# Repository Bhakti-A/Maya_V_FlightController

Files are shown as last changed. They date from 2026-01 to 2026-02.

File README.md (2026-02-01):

# Maya_V Flight Controller

This is a custom flight controller PCB designed for drones.

## PCB Preview

<p align="center">
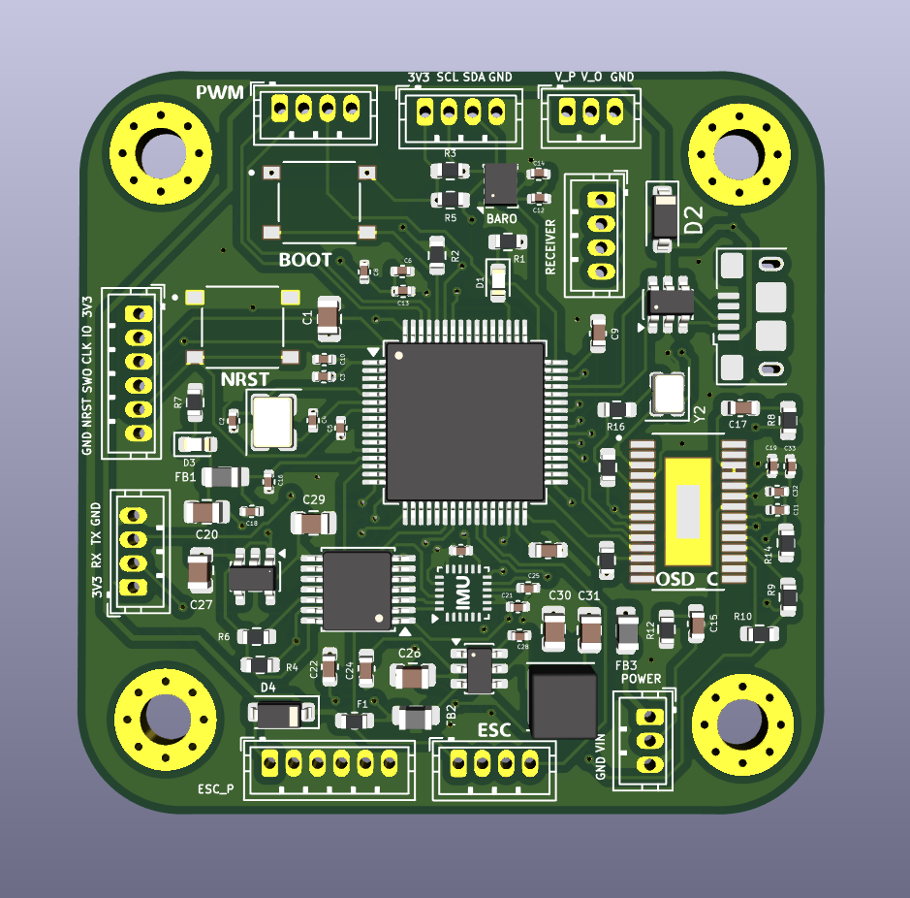
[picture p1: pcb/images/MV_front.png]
  
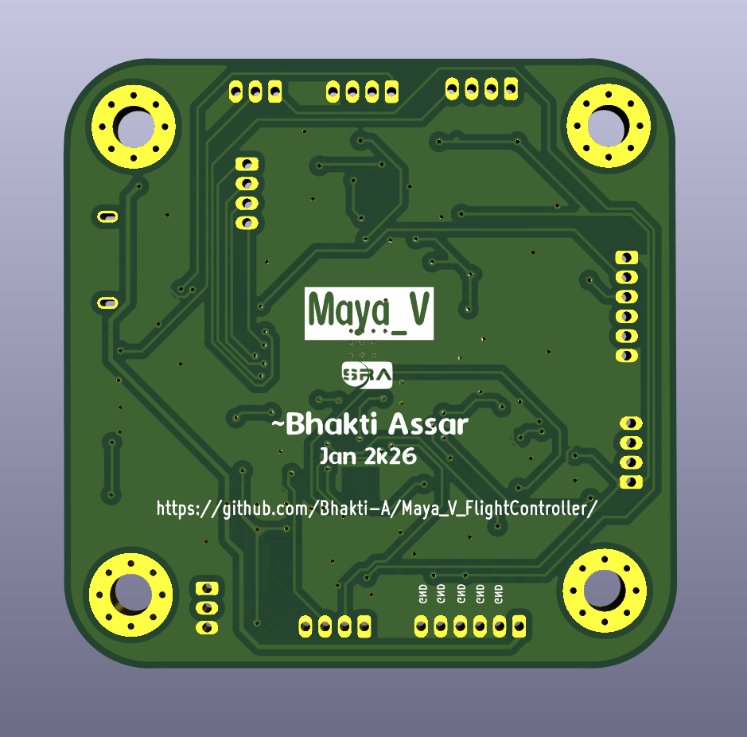
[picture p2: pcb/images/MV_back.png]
  
</p>

## Features

- **Microcontroller:** STM32F405  
- **IMU Sensor:** ICM-20948  
- **Barometer:** BMP280  
- **Video OSD:** MAX7456 
- **ESC Outputs:** 4× PWM channels (with extra PWM expansion)  
- **Communication Interfaces:** UART, I2C, USB  

## Hardware Design

### Schematic & PCB Layout
<p align="center">
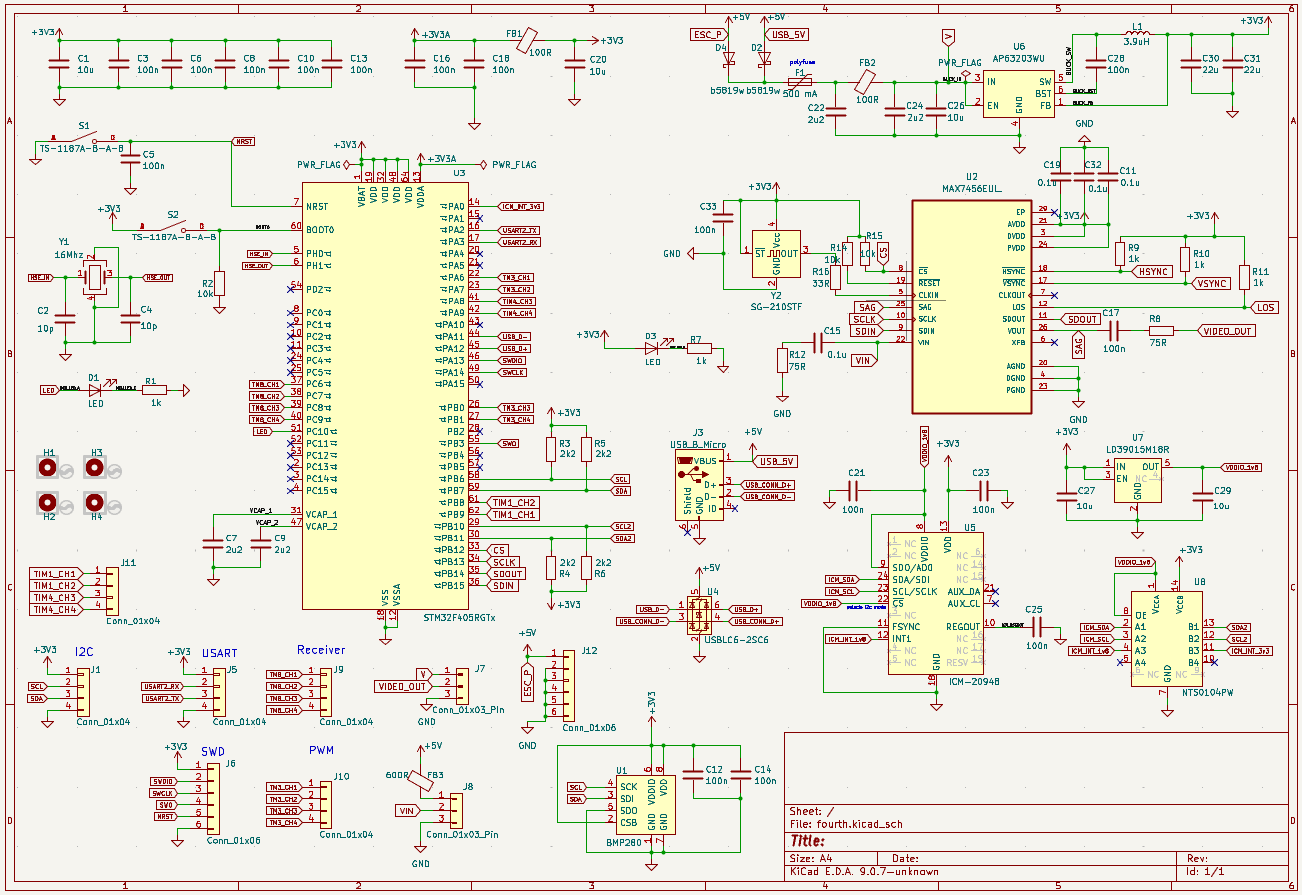
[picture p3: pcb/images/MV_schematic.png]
  
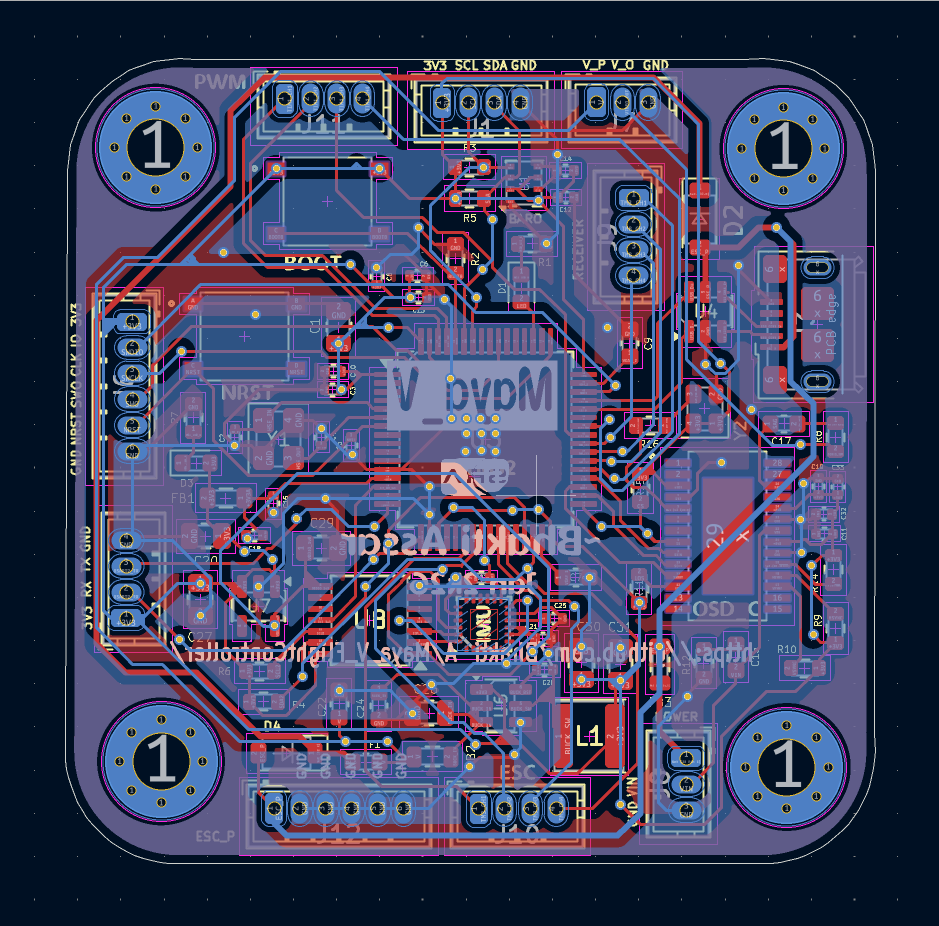
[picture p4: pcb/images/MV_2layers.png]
  
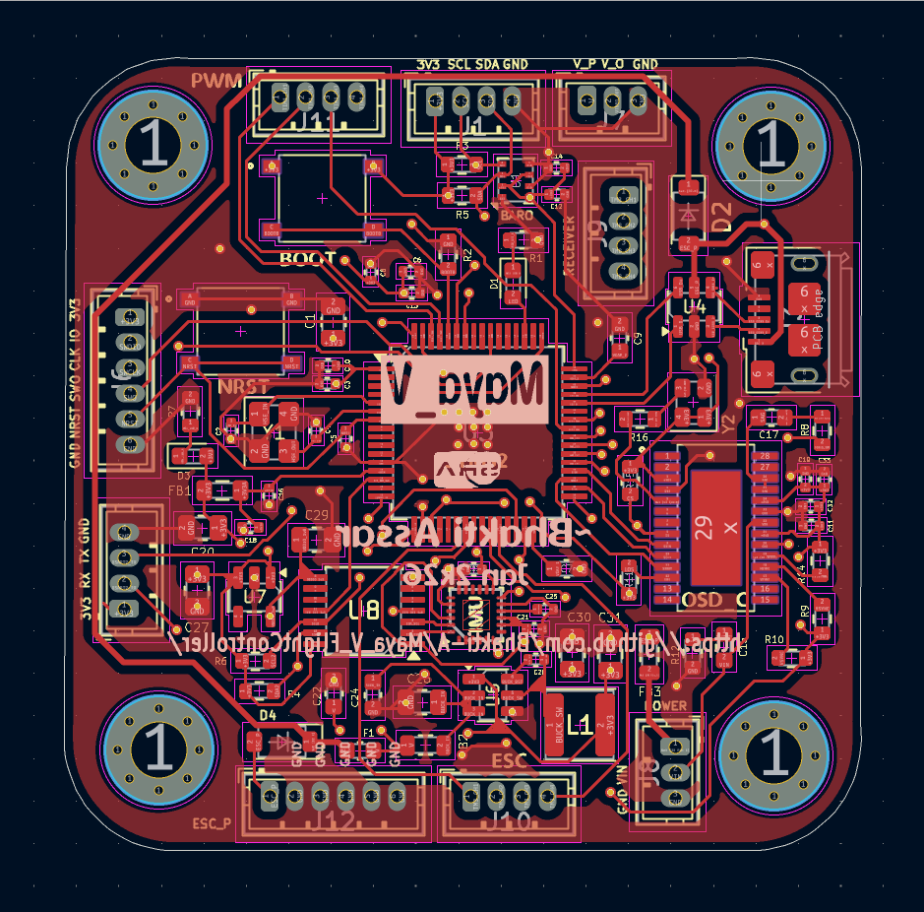
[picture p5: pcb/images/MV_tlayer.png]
  
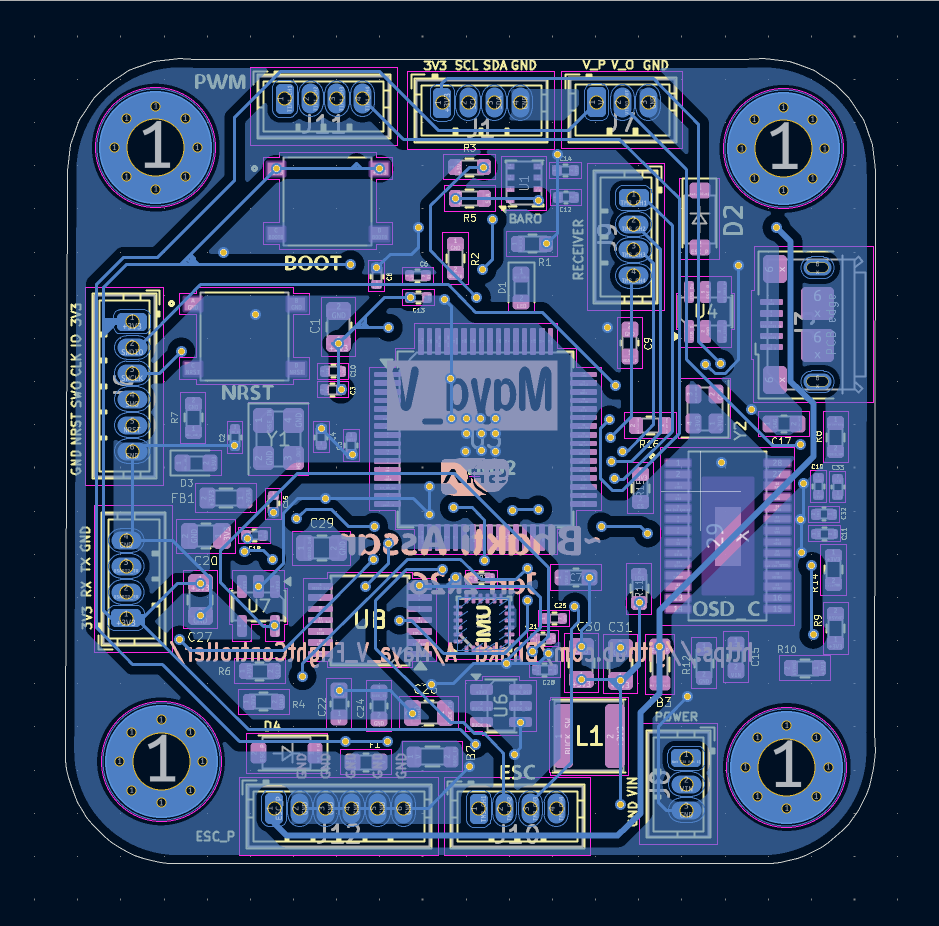
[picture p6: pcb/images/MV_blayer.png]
  
</p>

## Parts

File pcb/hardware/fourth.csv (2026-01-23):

Reference | Qty | Value | DNP | Exclude from BOM | Exclude from Board | Footprint | Datasheet
C1,C20,C26,C27,C29 | 5 | 10u |  |  |  | Capacitor_SMD:C_0805_2012Metric | ~
C2,C4 | 2 | 10p |  |  |  | Capacitor_SMD:C_0402_1005Metric | ~
C3,C5,C6,C8,C10,C12,C13,C14,C16,C18,C21,C23,C25,C28,C33 | 15 | 100n |  |  |  | Capacitor_SMD:C_0402_1005Metric | ~
C7,C9,C22,C24 | 4 | 2u2 |  |  |  | Capacitor_SMD:C_0603_1608Metric | ~
C11,C19,C32 | 3 | 0.1u |  |  |  | Capacitor_SMD:C_0402_1005Metric | ~
C15 | 1 | 0.1u |  |  |  | Capacitor_SMD:C_0603_1608Metric | ~
C17 | 1 | 100n |  |  |  | Capacitor_SMD:C_0603_1608Metric | ~
C30,C31 | 2 | 22u |  |  |  | Capacitor_SMD:C_0805_2012Metric | ~
D1,D3 | 2 | LED |  |  |  | LED_SMD:LED_0603_1608Metric | ~
D2,D4 | 2 | b5819w |  |  |  | Diode_SMD:D_SOD-123 | ~
F1 | 1 | 500 mA |  |  |  | Fuse:Fuse_0603_1608Metric | ~
FB1,FB2 | 2 | 100R |  |  |  | Inductor_SMD:L_0805_2012Metric | ~
FB3 | 1 | 600R |  |  |  | Inductor_SMD:L_0805_2012Metric | ~
H1,H2,H3,H4 | 4 | MountingHole |  | Excluded from BOM |  | MountingHole:MountingHole_3.2mm_M3_Pad_Via | ~
J1,J5,J9,J10,J11 | 5 | Conn_01x04 |  |  |  | Connector_PinSocket_2.00mm:PinSocket_1x04_P2.00mm_Vertical | ~
J3 | 1 | USB_B_Micro |  |  |  | Connector_USB:USB_Micro-B_Amphenol_10118193-0001LF_Horizontal | ~
J6,J12 | 2 | Conn_01x06 |  |  |  | Connector_PinSocket_2.00mm:PinSocket_1x06_P2.00mm_Vertical | ~
J7,J8 | 2 | Conn_01x03_Pin |  |  |  | Connector_PinSocket_2.00mm:PinSocket_1x03_P2.00mm_Vertical | ~
L1 | 1 | 3.9uH |  |  |  | Inductor_SMD:L_Sunlord_SWPA4030S | ~
R1,R7,R9,R10,R11 | 5 | 1k |  |  |  | Resistor_SMD:R_0603_1608Metric | ~
R2,R14,R15 | 3 | 10k |  |  |  | Resistor_SMD:R_0603_1608Metric | ~
R3,R4,R5,R6 | 4 | 2k2 |  |  |  | Resistor_SMD:R_0603_1608Metric | ~
R8,R12 | 2 | 75R |  |  |  | Resistor_SMD:R_0603_1608Metric | ~
R16 | 1 | 33R |  |  |  | Resistor_SMD:R_0603_1608Metric | ~
S1,S2 | 2 | TS-1187A-B-A-B |  |  |  | TS-1187A-B-A-B:SW_TS-1187A-B-A-B
U1 | 1 | BMP280 |  |  |  | Package_LGA:Bosch_LGA-8_2x2.5mm_P0.65mm_ClockwisePinNumbering | https://ae-bst.resource.bosch.com/media/_tech/media/datasheets/BST-BMP280-DS001.pdf
U2 | 1 | MAX7456EUI_ |  |  |  | MAX7456EUI_:SOP65P637X110-28N
U3 | 1 | STM32F405RGTx |  |  |  | Package_QFP:LQFP-64_10x10mm_P0.5mm | https://www.st.com/resource/en/datasheet/stm32f405rg.pdf
U4 | 1 | USBLC6-2SC6 |  |  |  | Package_TO_SOT_SMD:SOT-23-6 | https://www.st.com/resource/en/datasheet/usblc6-2.pdf
U5 | 1 | ICM-20948 |  |  |  | Sensor_Motion:InvenSense_QFN-24_3x3mm_P0.4mm | http://www.invensense.com/wp-content/uploads/2016/06/DS-000189-ICM-20948-v1.3.pdf
U6 | 1 | AP63203WU |  |  |  | Package_TO_SOT_SMD:TSOT-23-6 | https://www.diodes.com/assets/Datasheets/AP63200-AP63201-AP63203-AP63205.pdf
U7 | 1 | LD39015M18R |  |  |  | Package_TO_SOT_SMD:SOT-23-5 | http://www.st.com/resource/en/datasheet/ld39015.pdf
U8 | 1 | NTS0104PW |  |  |  | Package_SO:TSSOP-14_4.4x5mm_P0.65mm
Y1 | 1 | 16Mhz |  |  |  | Crystal:Crystal_SMD_3225-4Pin_3.2x2.5mm | ~
Y2 | 1 | SG-210STF |  |  |  | Oscillator:Oscillator_SMD_SeikoEpson_SG210-4Pin_2.5x2.0mm | https://support.epson.biz/td/api/doc_check.php?mode=dl&lang=en&Parts=SG-210STF

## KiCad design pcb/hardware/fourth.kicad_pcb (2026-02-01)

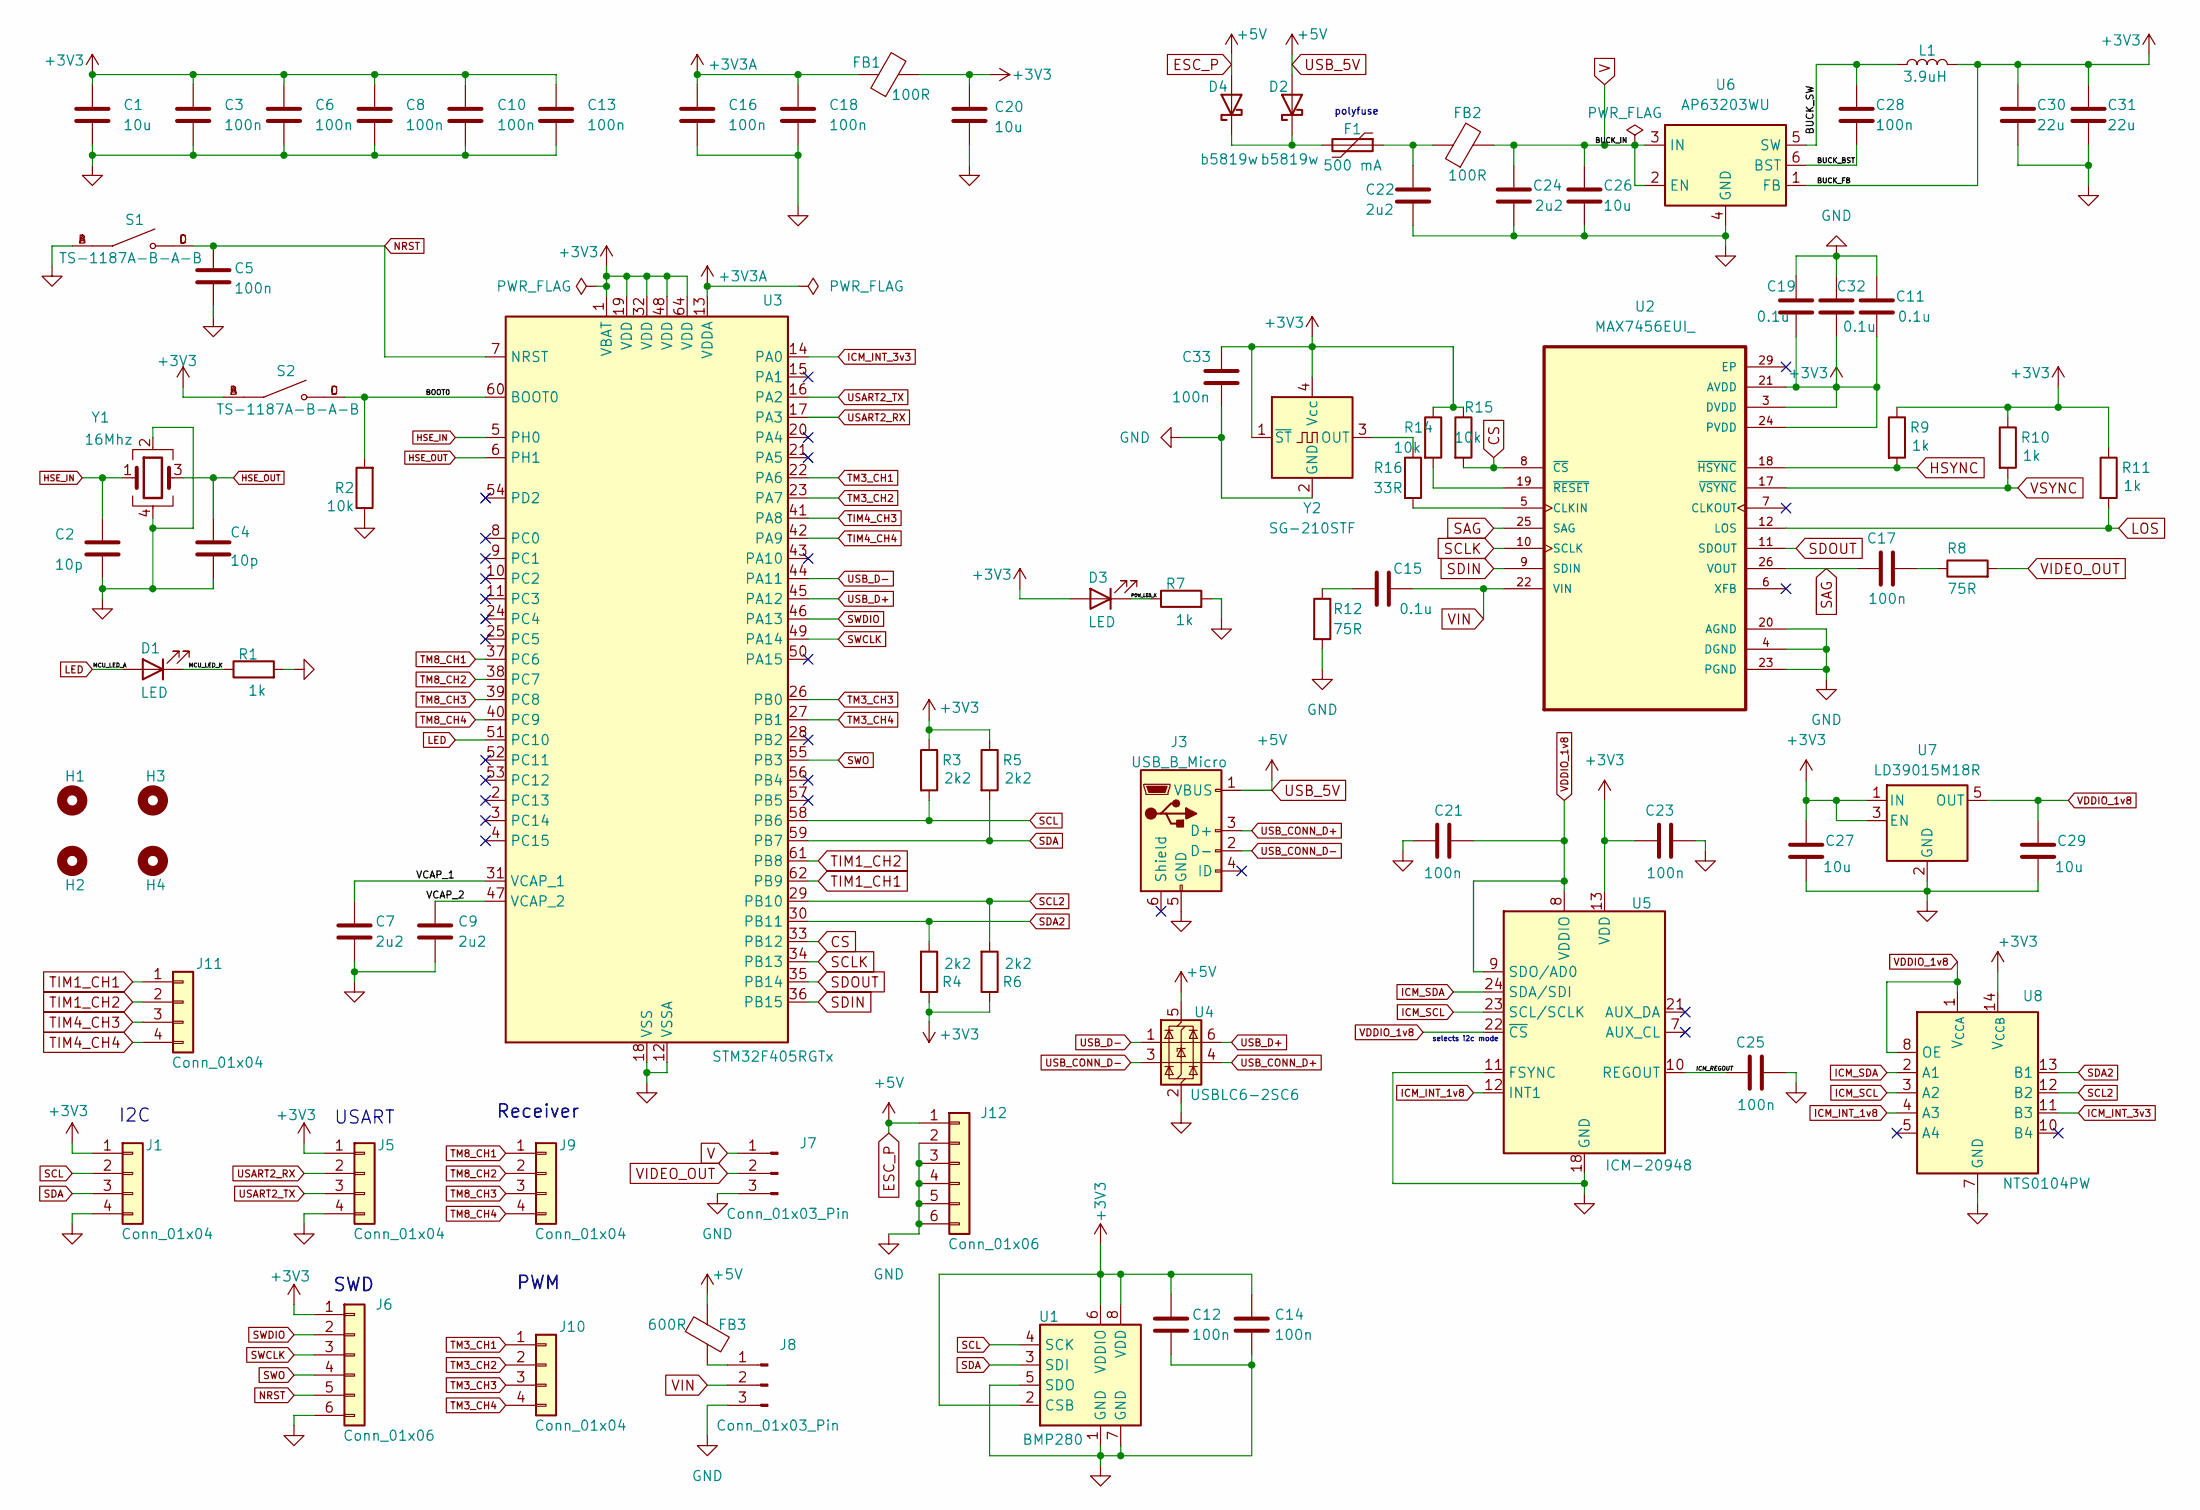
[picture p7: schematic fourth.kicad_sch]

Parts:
C1, C20, C26, C27, C29: 10u; C_0805_2012Metric
C2, C4: 10p; C_0402_1005Metric
C3, C5, C6, C8, C10, C12, C13, C14, C16, C18, C21, C23, C25, C28, C33: 100n; C_0402_1005Metric
C7, C9, C22, C24: 2u2; C_0603_1608Metric
C11, C19, C32: 0.1u; C_0402_1005Metric
C15: 0.1u; C_0603_1608Metric
C17: 100n; C_0603_1608Metric
C30, C31: 22u; C_0805_2012Metric
D1, D3: LED; LED_0603_1608Metric
D2, D4: b5819w; D_SOD-123
F1: 500 mA; Fuse_0603_1608Metric
FB1, FB2: 100R; L_0805_2012Metric
FB3: 600R; L_0805_2012Metric
H1, H2, H3, H4: MountingHole; MountingHole_3.2mm_M3_Pad_Via
J1, J5, J9, J10, J11: Conn_01x04; JST_ZH_B4B-ZR_1x04_P1.50mm_Vertical
J3: USB_B_Micro; USB_Micro-B_Amphenol_10118193-0001LF_Horizontal
J6, J12: Conn_01x06; JST_ZH_B6B-ZR_1x06_P1.50mm_Vertical
J7, J8: Conn_01x03_Pin; JST_ZH_B3B-ZR_1x03_P1.50mm_Vertical
L1: 3.9uH; L_Sunlord_SWPA4030S
R1, R7, R9, R10, R11: 1k; R_0603_1608Metric
R2, R14, R15: 10k; R_0603_1608Metric
R3, R4, R5, R6: 2k2; R_0603_1608Metric
R8, R12: 75R; R_0603_1608Metric
R16: 33R; R_0603_1608Metric
S1, S2: TS-1187A-B-A-B; SW_TS-1187A-B-A-B; PARTREV A0
U1: BMP280; Bosch_LGA-8_2x2.5mm_P0.65mm_ClockwisePinNumbering
U2: MAX7456EUI_; SOP65P637X110-28N
U3: STM32F405RGTx; LQFP-64_10x10mm_P0.5mm
U4: USBLC6-2SC6; SOT-23-6
U5: ICM-20948; InvenSense_QFN-24_3x3mm_P0.4mm
U6: AP63203WU; TSOT-23-6
U7: LD39015M18R; SOT-23-5
U8: NTS0104PW; TSSOP-14_4.4x5mm_P0.65mm
Y1: 16Mhz; Crystal_SMD_3225-4Pin_3.2x2.5mm
Y2: SG-210STF; Oscillator_SMD_SeikoEpson_SG210-4Pin_2.5x2.0mm

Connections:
+3V3: C1.1, C3.1, C6.1, C8.1, C10.1, C11.2, C12.1, C13.1, C14.2, C19.2, C20.1, C23.1, C27.1, C30.1, C31.1, C32.1, C33.1, D3.2 (A), FB1.2, J1.1, J5.1, J6.1, L1.2, R3.1, R4.1, R5.1, R6.1, R9.1, R10.1, R11.1, R14.1, R15.1, S2.A, S2.B, U1.2 (CSB), U1.6 (VDDIO), U1.8 (VDD), U2.3 (DVDD), U2.21 (AVDD), U2.24 (PVDD), U3.1 (VBAT), U3.19 (VDD), U3.32 (VDD), U3.48 (VDD), U3.64 (VDD), U5.13 (VDD), U6.1 (FB), U7.1 (IN), U7.3 (EN), U8.14 (V_{CCB}), Y2.1 (~ST), Y2.4 (Vcc)
+3V3A: C16.1, C18.1, FB1.1, U3.13 (VDDA)
/BOOT0: R2.2, S2.C, S2.D, U3.60 (BOOT0)
/BUCK_BST: C28.2, U6.6 (BST)
/BUCK_SW: C28.1, L1.1, U6.5 (SW)
/ICM_REGOUT: C25.1, U5.10 (REGOUT)
/MCU_LED_K: D1.1 (K), R1.1
/POW_LED_K: D3.1 (K), R7.1
/VCAP_1: C7.1, U3.31 (VCAP_1)
/VCAP_2: C9.1, U3.47 (VCAP_2)
CS: R15.2, U2.8 (~CS), U3.33 (PB12)
ESC_P: D2.2 (A), D4.2 (A), FB3.1, J3.1 (VBUS), J12.1, U4.5 (VBUS)
GND: C1.2, C2.2, C3.2, C4.2, C5.2, C6.2, C7.2, C8.2, C9.2, C10.2, C11.1, C12.2, C13.2, C14.1, C16.2, C18.2, C19.1, C20.2, C21.2, C22.2, C23.2, C24.2, C25.2, C26.2, C27.2, C29.2, C30.2, C31.2, C32.2, C33.2, J1.4, J3.5 (GND), J5.4, J6.6, J7.3, J8.3, J12.2, J12.3, J12.4, J12.5, J12.6, R1.2, R2.1, R7.2, R12.2, S1.A, S1.B, U1.1 (GND), U1.5 (SDO), U1.7 (GND), U2.4 (DGND), U2.20 (AGND), U2.23 (PGND), U3.12 (VSSA), U3.18 (VSS), U3.63 (VSS), U4.2 (GND), U5.11 (FSYNC), U5.18 (GND), U5.20 (GND), U6.4 (GND), U7.2 (GND), U8.7 (GND), Y1.2, Y1.4, Y2.2 (GND)
HSE_IN: C2.1, U3.5 (PH0), Y1.1
HSE_OUT: C4.1, U3.6 (PH1), Y1.3
HSYNC: R9.2, U2.18 (~HSYNC)
ICM_INT_1v8: U5.12 (INT1), U8.4 (A3)
ICM_INT_3v3: U3.14 (PA0), U8.11 (B3)
ICM_SCL: U5.23 (SCL/SCLK), U8.3 (A2)
ICM_SDA: U5.24 (SDA/SDI), U8.2 (A1)
LED: D1.2 (A), U3.51 (PC10)
LOS: R11.2, U2.12 (LOS)
NRST: C5.1, J6.5, S1.C, S1.D, U3.7 (NRST)
unnamed: C15.1, R12.1
unnamed: C17.2, R8.1
unnamed: D2.1 (K), D4.1 (K), F1.2
unnamed: FB3.2, J8.1
unnamed: R16.2, U2.5 (CLKIN)
unnamed: R14.2, U2.19 (~RESET)
unnamed: R16.1, Y2.3 (OUT)
SAG: C17.1, U2.25 (SAG), U2.26 (VOUT)
SCL: J1.2, R3.2, U1.4 (SCK), U3.58 (PB6)
SCL2: R6.2, U3.29 (PB10), U8.12 (B2)
SCLK: U2.10 (SCLK), U3.34 (PB13)
SDA: J1.3, R5.2, U1.3 (SDI), U3.59 (PB7)
SDA2: R4.2, U3.30 (PB11), U8.13 (B1)
SDIN: U2.9 (SDIN), U3.36 (PB15)
SDOUT: U2.11 (SDOUT), U3.35 (PB14)
SWCLK: J6.3, U3.49 (PA14)
SWDIO: J6.2, U3.46 (PA13)
SWO: J6.4, U3.55 (PB3)
TIM1_CH1: J11.1, U3.62 (PB9)
TIM1_CH2: J11.2, U3.61 (PB8)
TIM4_CH3: J11.3, U3.41 (PA8)
TIM4_CH4: J11.4, U3.42 (PA9)
TM3_CH1: J10.1, U3.22 (PA6)
TM3_CH2: J10.2, U3.23 (PA7)
TM3_CH3: J10.3, U3.26 (PB0)
TM3_CH4: J10.4, U3.27 (PB1)
TM8_CH1: J9.1, U3.37 (PC6)
TM8_CH2: J9.2, U3.38 (PC7)
TM8_CH3: J9.3, U3.39 (PC8)
TM8_CH4: J9.4, U3.40 (PC9)
USART2_RX: J5.2, U3.17 (PA3)
USART2_TX: J5.3, U3.16 (PA2)
USB_CONN_D+: J3.3 (D+), U4.4 (I/O2)
USB_CONN_D-: J3.2 (D-), U4.3 (I/O2)
USB_D+: U3.45 (PA12), U4.6 (I/O1)
USB_D-: U3.44 (PA11), U4.1 (I/O1)
VDDIO_1v8: C21.1, C29.1, U5.8 (VDDIO), U5.9 (SDO/AD0), U5.22 (~CS), U7.5 (OUT), U8.1 (V_{CCA}), U8.8 (OE)
VIDEO_OUT: J7.2, R8.2
VIN: C15.2, J8.2, U2.22 (VIN)
VSYNC: R10.2, U2.17 (~VSYNC)

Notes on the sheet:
PWM
SWD
selects i2c mode
USART
polyfuse
Receiver
I2C

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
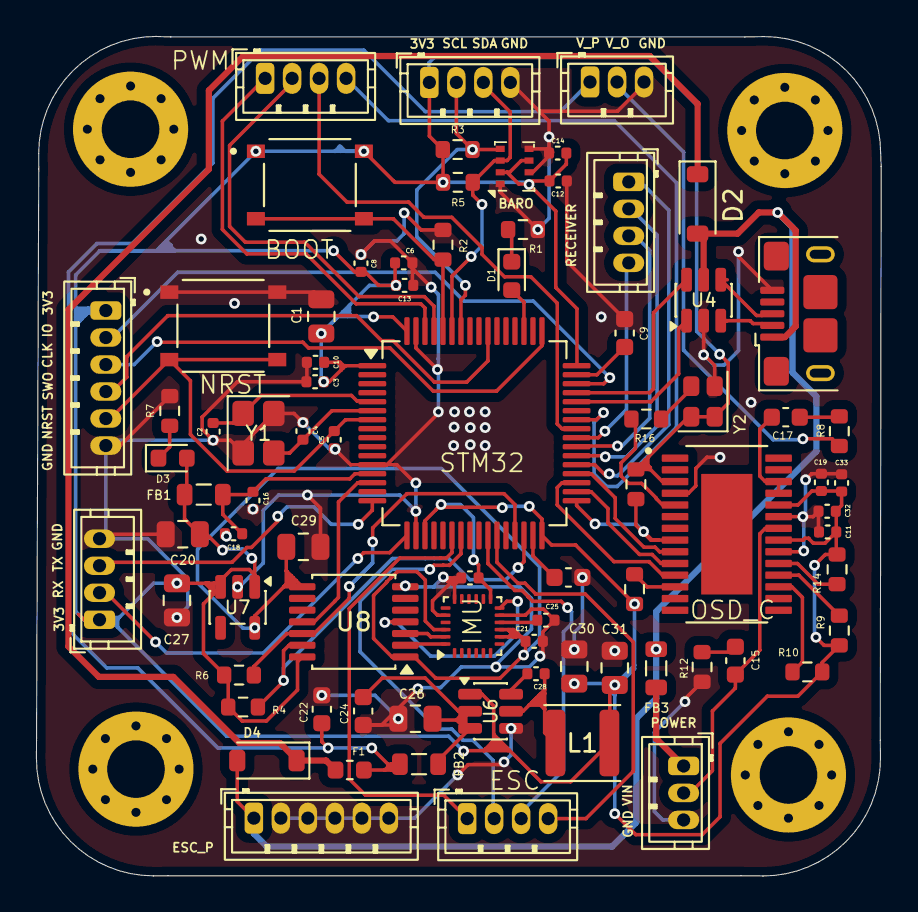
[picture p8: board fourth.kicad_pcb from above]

Board: 2 copper layers, 46.9 x 46.6 mm, 83 parts (0 on the bottom side), 65 nets.

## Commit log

2026-01-23 PCB files and README
    [fourth.csv, fourth.kicad_pcb, fourth.kicad_sch]
2026-02-01 Update pcb
    [fourth.csv, fourth.kicad_pcb, fourth.kicad_sch]
